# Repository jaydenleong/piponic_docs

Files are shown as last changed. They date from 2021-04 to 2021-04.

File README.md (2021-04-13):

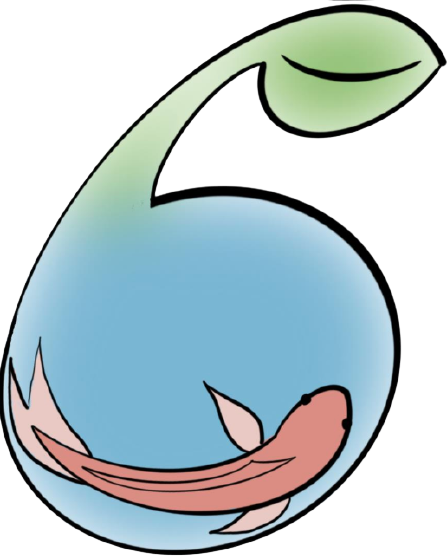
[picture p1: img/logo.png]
#  piponic_docs

## Project Description

This project aims to reduce urban food insecurity by reducing the cost and labour requirements of monitoring aquaponic or hydroponic food-growing systems. Designed specifically for hobbyist or small-scale growers, our project monitors critical system variables such as pH, temperature, and water-level and provides autonomous control. Critical notifications, real-time information, control settings, and system-history is available to users on a mobile application. 

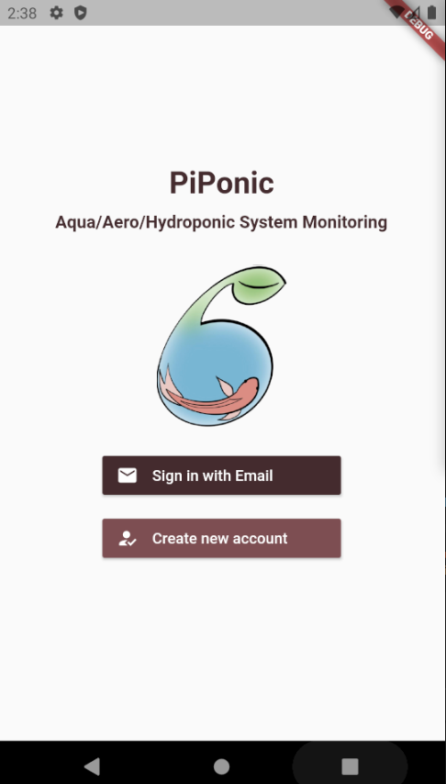
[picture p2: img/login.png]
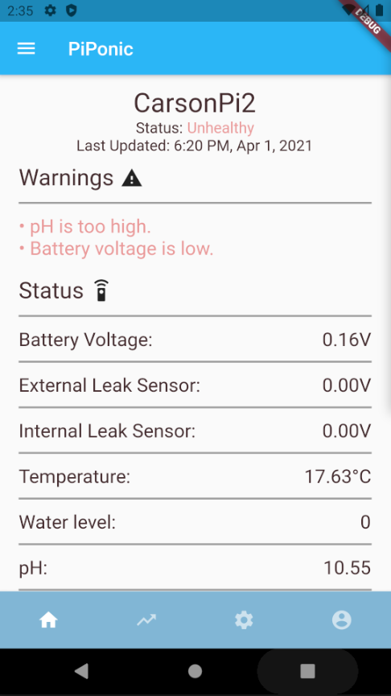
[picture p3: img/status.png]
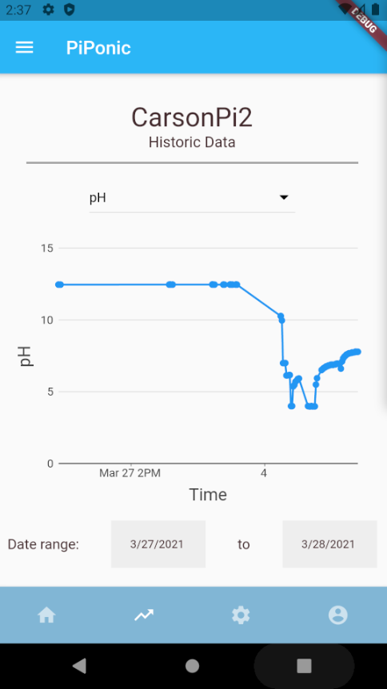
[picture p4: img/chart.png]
 &nbsp;&nbsp;&nbsp;  &nbsp;&nbsp;&nbsp; 

Our work contributes a low-cost, open-source hardware design, and IoT development framework that will allow hobbyists to expand and modify the system for their own needs. By simplifying the communication protocols, growers can focus on adding new sensors instead of worrying about data-security. 

Our system can also operate on battery power in the event of a power-outage, a critical failure in aquaponic systems. This feature allows growers to be notified and to begin to take corrective action within the minute of the outage.

## This Repository

Contains key documents describing our project. This includes the following (in the `docs/` folder): 

- System Installation
- User Manual
- Requirements
- Design
- Verification and Validation

Please consult those documents for more information about the project.

It also contains hardware modelling files, including: 
- Solidworks 2019 enclosure models (for layout)
- Altium Designer 2019 PCB and associated schematic files
- Gerber files associated with PCB design
- Bill of materials for PCB components

## Related Repositories

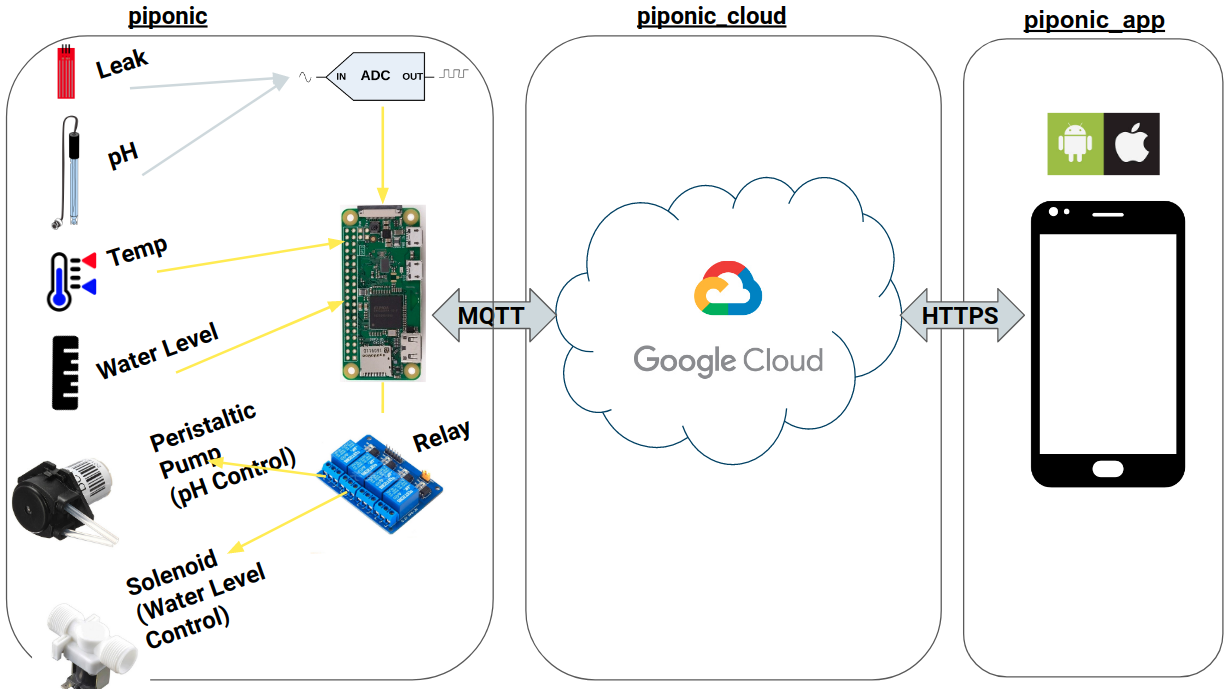
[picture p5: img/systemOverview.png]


- [piponic](https://github.com/jaydenleong/piponic): A sensing and control system for aquaponics or hydroponics. Runs on a Raspberry Pi and connects to the mobile application using this repository.
- [piponic_cloud](https://github.com/jaydenleong/piponic_cloud): Google Firebase functions that connect Raspberry Pis and the mobile application.
- [piponic_app](https://github.com/jaydenleong/piponic_app): The mobile application for users to remotely monitor and control their aqua/hydroponic installation. Implemented using Google's Flutter.

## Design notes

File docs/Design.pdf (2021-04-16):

# IoT Monitoring of Aquaponic and

# Hydroponic Food Production

# Design

### UBC Electrical and Computer Engineering Capstone 121

Carson Berry

Lynes Chan

Mason Duan

Jayden Leong

Hannah Xu

for

UBC SEEDS Sustainability Program

Bernhard Nimmervoll, UBC Mechanical Engineering

### April 16, 2021

## Revision History

Date | Author | Sections | Change
2020-10-05 | JL | 1.0 - 2.0 | Creation of document skeleton
2020-10-30 | JL | 1.0 - 5.0 | Added system overview and skeleton of subsystem sections
2020-11-29 | LC | 3.0 - 4.0 | Added the design decisions made for the sensors and the control devices
2021-02-19 | CB | 3.0 - 4.0 | Added details about power architecture, sensors, mounting, hardware, heat management
2021-02-20 | JL | 1.0 - 2.0 | Updated system overview to add brief overview of hydroponics and aquaponics, new system di-agram and updated purpose. Updated IoT sec-tion with details about the cloud implementation, along with other minor edits to microcomputer section.
2021-02-20 | MD | 6.0 | Updated software section to include use case di-gagram, screen explanations, and how the mobile application interacts with the back end.
2021-04-11 | CB | 3.0-4.0, 7.0 | Updated power design, sensor firmware, hardware design, added BOM tables, and ordering informa-tion.
2021-04-12 | JL | 1.0-2.0 | Added references and further detail to overview and background sections. Updated IoT section with references and implementation details.
2021-04-14 | MD | 6.0 | Updated software section to include final use case diagram design, screen explanations, and how the mobile application interacts with the back end.

## Contents

1 System Overview | 5
2 Internet of Things (IoT) | 8
3 Power | 15
4 Sensors | 18

5 Control Systems | 22
6 Software Application | 24
7 Circuit Integration - PCB | 33
8 Assembly | 34
9 Bill of Materials | 36

## 1 System Overview

Since our project is designed to work with both hydroponic and aquaponic systems, this section provides an brief introduction to both hydroponics and aquaponics. Afterward, the purpose of this project is given, and the high-level system design is described.

### 1.1 Hydroponics and Aquaponics

Hydroponics is a method of agriculture where plants are grown in a nutrient-rich aqueous solution [1]. Nutrients in hydroponics are inputted by the grower into the aqueous solution to nourish plants. This contrasts traditional forms of agriculture, where plants are grown in soil.

Aquaponics is very similar to hydroponics. In aquaponics, plants are also grown in an aqueous solution, however plants recieve nutrients in a different manner. Instead of growers inputting nutrients, plants recieve nutrients from fish waste [2]. To make this possible, fish are grown in separate tanks from the plants, with a filtration tank, and sump tank between them. Aquaponics recieves its name because of this, by being a mixture of aquaculture and hydroponics. A simplified diagram of aquaponics is show in Figure 1. Note that hydroponics systems look nearly the same, minus the fish tank.

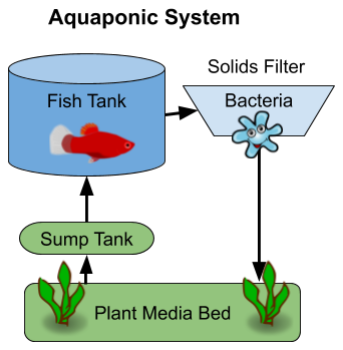
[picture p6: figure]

Figure 1: A diagram of a basic aquaponics system

### 1.2 Project Purpose

The goal of our project is to develop a system to monitor and control critical variables for hydroponic and aquaponic systems. In particular, our project focuses on monitoring water variables as they are most difficult to maintain at healthy levels in aquaponic and hydroponic systems. These variables include water pH, level, leakage, and temperature.

In terms of users, this system will be designed for small scale and hobbyist growers who maintain their aquaponic or hydroponic systems. Note that for this project, small-scale aquaponics or hydroponic systems are defined as systems with under 200 plants and under 3000 gallons of water. Since our users are small-scale growers and hobbyists, the system will utilize open-source and low cost technologies wherever possible to minimize barriers to usage and replication.

Please refer to the included Requirements document for further details about system requirements, background, and purpose.

### 1.3 High-Level System Design

Figure 2 below provides an overview of our design. As you can see, our design contains the following four subsystems: sensors, control, Cloud, and software application.

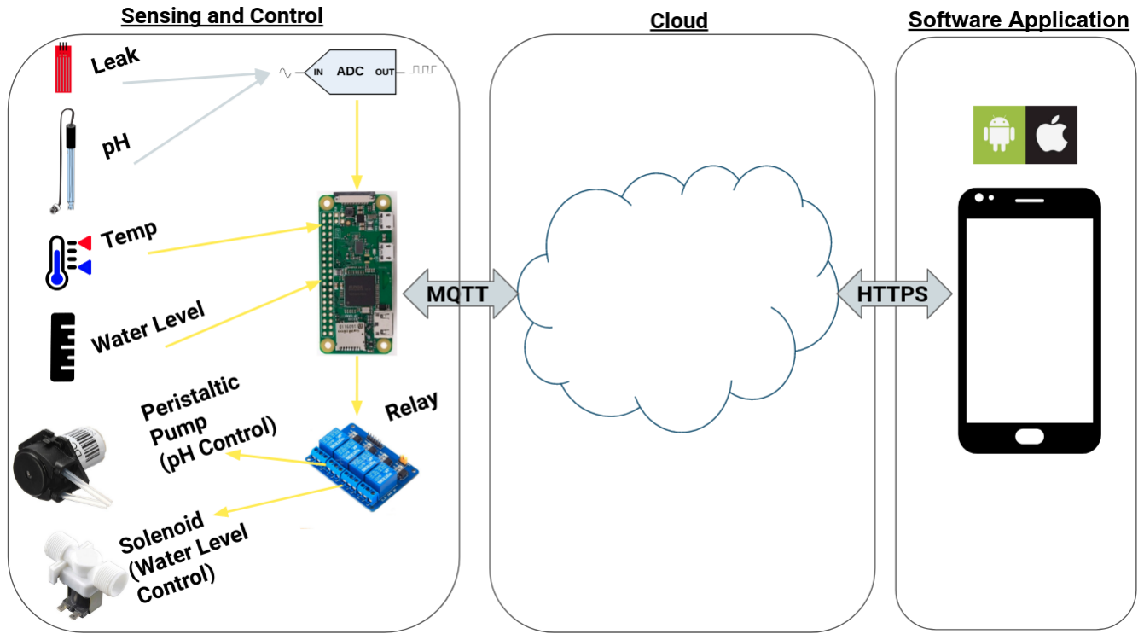
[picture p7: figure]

Figure 2: System Level Block Diagram

First, we can see the sensing and control subsystems in the “Sensing and Control”

block in Figure 2. This consists of a microcomputer attached to multiple sensors and control devices. As previously mentioned, there are four key sensors in our project shown: the water leakage, pH, temperature, and level sensors. These sensors allow our design to take measurements of the water of aquaponics or hydroponics systems. As such, the pH, temperature, and water level sensors are placed inside water tanks in an aquaponic or hydroponic system. As far as the control systems are concerned, two devices are attached to the microcomputer: a peristaltic pump and a solenoid. These two devices allow our design to automatically adjust pH and water level respectively.

Next, the Cloud subsystem is shown in “Cloud” block in Figure 2. This system’s responsibility is to transfer data between a mobile software application and the sensing and control system. It also stores past sensor measurements for later analysis.

Finally, on the software application is show in the “Software Application” block in Figure 2. This is where the user primarily interacts with their hydroponic or aquaponic system. This application displays past and current sensor measurements. It also allows the user to recieve alerts if urgent issues are detected by the sensing and control system, including issues like power failure and dangerous water pH levels.

In the following sections, the design of each of these subsystems will be explored in further detail.

## 2 Internet of Things (IoT)

The IoT subsystem recieves its name from the design decision to use internet communication to communicate with sensors and control devices installed on aquaponics or hydroponic systems. This enables our design to leverage advantages of internet communications. One key advantage is that the vast majority of our users have internet connected devices including laptops and mobile phones. Another key advantage is the ability for growers to monitor and control their aquaponics systems from anywhere they have internet connectivity.

The IoT subsystem, in our project, refers to all hardware and software needed to communicate between sensors and output devices and the software application. See Figure 3 for an overview of our IoT subsystem design.

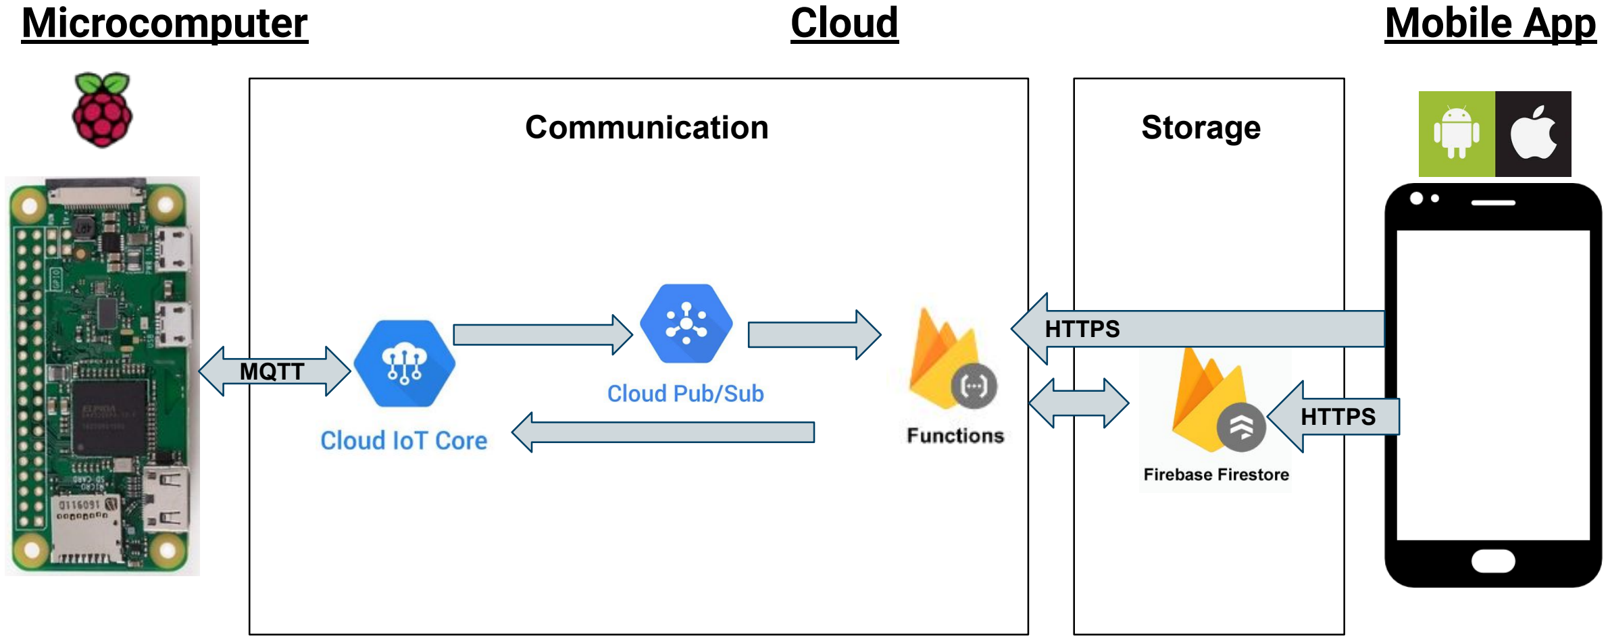
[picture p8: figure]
Microcomputer; Cloud; Mobile App; HTTPS; MQTT; Communication; Storage

Figure 3: IoT system overview

As seen in Figure 3, our IoT subsystem has 3 major components: the microcomputer, cloud, and mobile devices. The microcomputer and cloud components will be discussed in detail within this section. In the Software Application section, the mobile app component will be discussed further.

### 2.1 Microcomputer

There are two key functions that the microcomputer serves in our design. The first responsibility is to receive data from sensors, and to control output devices. The second responsibility is to send sensor readings to users, and to recieve commands for output devices from users. For each of these key functions, our team has made chosen design solutions to help address these issues. Consult Table 1 for a description of the key functions and their associated technological strategies.

Table 1: Description of microcomputer key functions and design strategies
Key Function | Req(s) | Design Solution | Reason(s)
Communicate with sensors and output devices | F1, F4 | Wired connection (e.g. SPI, IIC, GPIO), or wireless connection (e.g Bluetooth) depend-ing on the sensor or con-trol device | • Allows the flexibility to in-terface with many different sensors and output devices.
Communicate with user devices | F1, F2, F3, F6 | WiFi internet network connection | • Low cost compared other alternatives like LTE • High accesibility as hobby-ist and small-scale growers typically have a WiFi net-work setup within range of their system.

With these key functions in mind, our team selected a capable microcomputer. This microcomputer is the Raspberry Pi Zero W [3], shown in Figure 4.

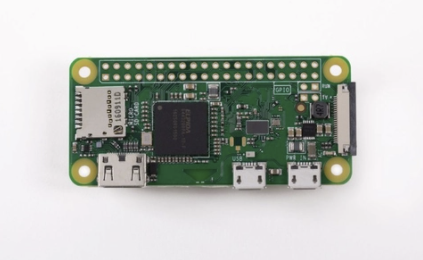
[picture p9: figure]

Figure 4: The Raspberry Pi Zero W microcomputer

The Raspberry Pi Zero W was chosen over other microcomputers that could perform the same key functions. This was done for the following reasons:

1. Low cost: costs around 40 CAD.
2. Wireless networking: supports both WiFi and Bluetooth.
3. Versatile: runs a Linux-based operating system called Raspberry Pi OS.
4. Documentation and support: Raspberry Pi is a popular platform with extensive tutorials, resources, and forums.
5. Interfacing: supports a variety of wired protocols including SPI, I2C. Also has 40 GPIO pins to interface with multiple devices.

Other notable microcomputers that were considered ESP32-based microcontrollers, and the Raspberry Pi 3B. However, the ESP32 was not chosen due to its more limited documentation and inability to run a linux-based operating system (making development slower). The Raspberry Pi 3B was not selected because of its similar functionality to the Raspberry Pi Zero W, but its higher cost of about 80 CAD.

Nevertheless, a final benefit of chosing a Raspberry Pi Zero W is that its software is compatible with other Raspberry Pi models, like the 3B. This gives design flexibility to optionally use more powerful or improved Raspberry Pi models other than the Raspberry Pi Zero W.

### 2.2 Cloud

The Cloud component of our IoT subsystem sits in between the microcomputer. Cloud in our project refers to cloud computing. This constitutes all the internet connected servers and associated IT infrastructure needed to communicate between the microcomputer (MCU) and the user’s mobile devices. As such, the cloud is responsible for the following:

- Relaying information between the MCU and user’s mobile devices
- Storing past sensor measurements
- Providing a software interface to the user’s mobile devices so they can access past sensor data and communicate with the MCU.
- Scaling to allow monitoring and control of multiple aquaponics or hydroponics systems from a single mobile device.

As such, the cloud contributes to meeting the functional requirements F1, F2, F3, and F6. Please refer to the Requirements document for details about these requirements.

As far as design solutions are concerned, we considered 2 key alternatives based on the above specifications. The first was using IT infrastructure as a cloud proxy to communicate between the microcomputer and the mobile application. The second choice was to communicate directly with the MCU, without any infrastructure in between. These options are summarized in Figure 5.

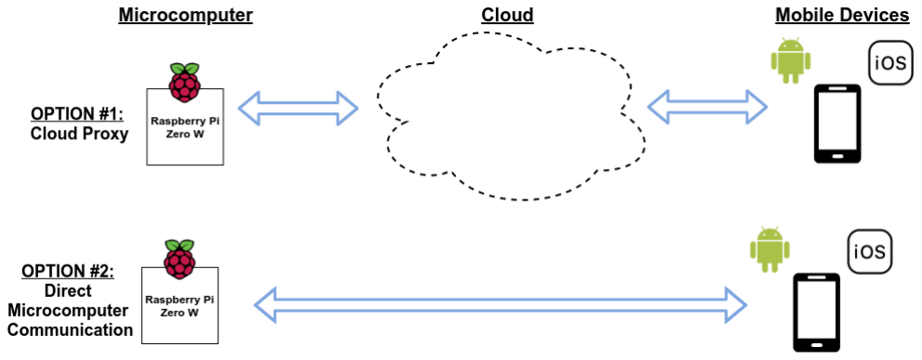
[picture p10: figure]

Figure 5: Two MCU to mobile application communication options.

To decide between these two main options, we weighed their strengths and weaknesses relative to their key functions. This comparison is summarized in Table 2.

Table 2: Comparison of MCU to mobile application communication options.
Function | Cloud Proxy | Direct MCU communication
Relaying information between the MCU and user’s mobile devices | Advantage: User devices can communicate the MCU anywhere with internet connectivity. | Advantage: No cost for proxy service. Disadvantage: User devices must be on the same local network as the microcomputer.
Storing past sensor measurements | Advantage: Cloud proxy services can automatically provision data storage to meet unlimited demand inexpensively. | Disadvantage: Users must be on the same local network as the MCU to access data.
Providing a software interface to the user’s mobile devices | Advantage: Cloud proxy services can offer APIs and pre-built tools to connect with mobile devices. | Advantage: communicating directly with an MCU can reduce software interface complexity and maintenance.
Scaling to allow monitoring and control of multiple aquaponics or hydroponics systems. | Advantage: Cloud proxy services offer automatic provisioning of resources based on demand | Disadvantage: limited to monitoring only systems on the same local network.

As seen in Table 2, the advantages of the cloud proxy option outweigh the direct MCU communication option. Most notably, the cloud proxy option offers more flexibility as it is not limited to being on the same private network as the MCU. It also is more capable of storing large amounts of past sensor data.

After choosing to use the cloud proxy option, we had a choice between 3rd party service providers, or managing our own cloud computing resources. We ultimately chose to use 3rd party IoT service providers over managing our own cloud computing resources for the following reasons:

1. Low cost: The estimated cost is less than 5 CAD/month.
2. High implementation speed: Service providers manage cloud computing resources, instead of developers needed to create and manage these from scratch.
3. Easy maintainance: Service providers typically provide web consoles for easy maintainability of resources.
4. Automatic scalability: Service providers automatically scale resources to match the amount of usage. For instance, more memory in a database is automatically provisioned.

Some popular 3rd party IoT service providers include Microsoft Azure, Google Cloud IoT, and Amazon Web Services (AWS) IoT. These service providers offer very similar services at comparable prices. So, our team decided to develop using Google Cloud IoT because it offered a better software interface to our mobile application.

This software interface will be discussed in further detail in the following sections. In addition, the architecture of our cloud system will be described in terms of two aspects: cloud communication and cloud storage.

### 2.2.1 Cloud Communication

Referring back to Figure 3, we see that the cloud communication component transfers data between the MCU and cloud storage. These components therefore help satisfy the functional requirements F1, F2, and F3, which require communication between the mobile application and the sensing and control system.

From Figure 3, we also see that the cloud commmunication part is made of 2 key components which are Google Cloud services. These are Google IoT Core, Google Cloud Pub/Sub, and Google Firebase Cloud Functions. See Table 3 below to see the role of each of these services in our design.

Table 3: Roles of Google Cloud communication services used.
Google Cloud Service | Role
IoT Core | • Provides an API for MCUs to communicate with Google Cloud using the MQTT protocol. • Provides MCU authentication and data encryption using public/private RSA keys
Pub/Sub | • Automatically recieves incoming messages from Google Cloud IoT core. • Allows Google Firebase Cloud Functions to respond to each message that is published by an MCU.
Firebase Functions | • Provides the ability to write functions that run on Google managed servers. • Writes MCU messages (with sensor data) in databases. These messages can then be retrieved by the mobile application. • Sends commands to MCUs through Google IoT Core.

Lastly, note that the communication protocol used between the MCU and Google Cloud IoT Core is MQTT. This was chosen over other possible protocols like HTTPs as it uses lower bandwidth and has less software overhead [4]. These two factors decrease the power consumption and data usage of our design.

### 2.2.2 Cloud Storage

Referring back to Figure 3, we see that the cloud storage components saves messages from both the MCU and the mobile application.

The key requirement satisfied by this section is F2, to be able to store past sensor measurements for analysis. However, like the previous section, the satisfy the functional requirements F1, and F3, which require communication between the mobile application and the sensing and control system.

Table 4 also shows another Google services that are used in our design: Google

Firebase Firestore.

Table 4: Roles of Google data storage services used.
Google Service | Role
Firebase Firestore | • Stores sensor measurements in a NoSQL format. • Stores MCU configurations.

Google Firestore is used for storage of past sensor measurements. This is because Google Firestore charges a cheaper rate for storage than other Google databases, making it preferable for storing large amounts of sensor measurement data [5]. It allows features a subscription model where new sensor readings are updated within our app as soon as they are stored in Firestore [6]. This allows us to display most recent sensor updates in near real-time.

Google Firestore also stores MCU configurations. When these configurations are updated, Google Cloud Functions automatically updates a device configuration. This is used to send commands to the sensing and control system from the mobile application. This design was chosen as it allows the mobile application to both read the current MCU configuration, and change it. That way, the mobile application can make configuration updates based on a MCU’s current status. For instance, if the pH level of a given MCU configuration is below the target value, it could be changed to a higher value by updating that MCU’s configuration.

### 2.2.3 Cloud System Implementation

As mentioned in section 2.2.1 above, Google Firebase Cloud Functions are used to save sensor messages, and connect IoT devices to the mobile application. So, just as depicted in Figure 3, Google Firebase Cloud Functions are central to the cloud system and define much of its functionality.

The implementation of this project’s Google Firebase Cloud Functions can be found in the piponic cloud repository (https://github.com/jaydenleong/piponic_cloud). The README of this repository also provides further documentation about how the overall cloud system can be setup and maintained.

## 3 Power

Our system is comprised of various electric components, including the Raspberry Pi microcomputer, sensors, and output devices. Power for the system will be available from two sources, a main, and a backup. The main power source is 12V DC. This is supplied by a commercially available power supply that rectifies and steps-down voltage coming from a 120V wall outlet. This will provide power to the sensor hub during normal operation. That is, when the device is plugged in, and the line-voltage is available.

### 3.1 Back-up Power

The backup power will be provided by a battery pack with 2 AA batteries, with voltage boosted to 5 V from a DC-DC boost converter. The arrangement of these two inputs can be seen in figure 6. 3 AA batteries could also be used in series to produce a voltage of 4.5V, which will increase the lifespan of the back-up power system and the efficiency of the boost-converter chip. If this arrangement of batteries is used, a voltage divider must be added to the battery-voltage monitoring circuit, so that the maximum voltage of 4.5V is read at max 3.3V. We recommend using 100k and 36.9k resistors for this voltage divider to minimize power loss.

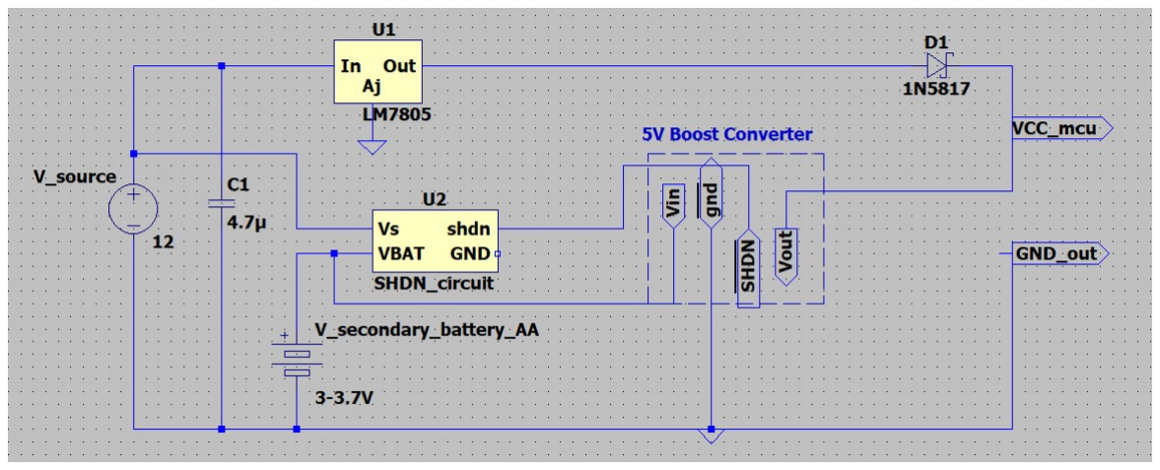
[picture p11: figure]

Figure 6: Uninterruptible power supply architecture.

The LM7805 voltage regulators are responsible for delivering all of the current used by the 5V devices during normal operation. It has been observed that all of the 5V devices consume around 200mA during normal operation, and the voltage regulators are rated to 1A. To increase the safety margin associated with heat-burnout, a 15g aluminum TO-220 heat sink was added to the LM7805 chip. Two LM7805 regulators are used in parallel to ensure adequate power is always available. This was also added to the Schottky diode at the output of the LM7805 chip.

To conserve the battery-lifespan, the boost converter is turned off automatically when the 12V line voltage is present. The circuit that accomplishes this can be seen in figure 7 - a simple BJT switch application. In the event of a power failure, the system will be able to run for 8 hours on backup power. This functionality is intended as a way to keep monitoring the condition of the aquaponic or hydroponic systems in the event of a power failure.

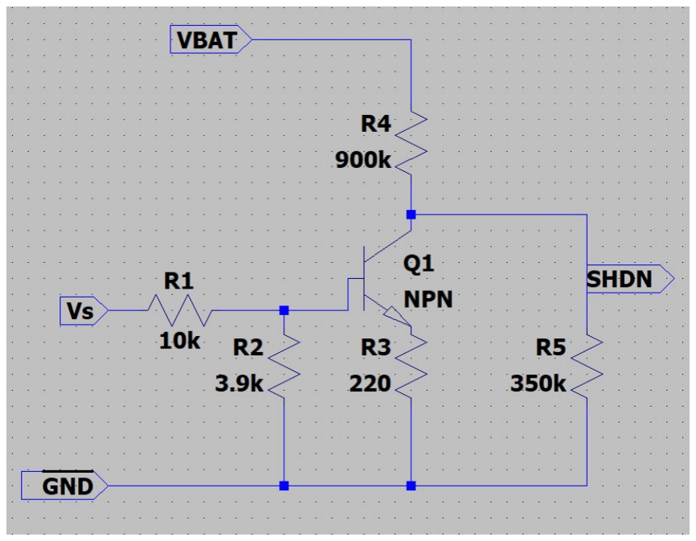
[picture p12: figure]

Figure 7: Boost converter shutdown circuit. This circuit disables the AA batteries when 12V is present.

For boosting 2 AA batteries up to 5 V, the Pololu 5V Step-Up Voltage Regulator U1V11F5 is a high quality, low cost, easily accessible option that can be implemented by hobbyists with minimal difficulty. It can take anywhere between 0.5 and 5 V input and will automatically boost it to 5.02 V output.

### 3.2 Power Budget

Our monitoring system consumes on average 810 mW when on back-up power. Most of this comes from the operation of the raspberry pi. A breakdown of the average power use can be seen in figure 8.

The control devices and relays operate only when line power is available (that is, when not on back-up power), and when all control devices are active the system consumes an additional 5W.

### 3.3 Current Protection

The output voltage will be connected via Schottky diode to the line voltage in, before being connected to the Raspberry Pi. This will effectively OR the voltage source seen by the Raspberry Pi. Several other circuit topologies were simulated and tested, and the Schottky diode topology represents the best functionality in both

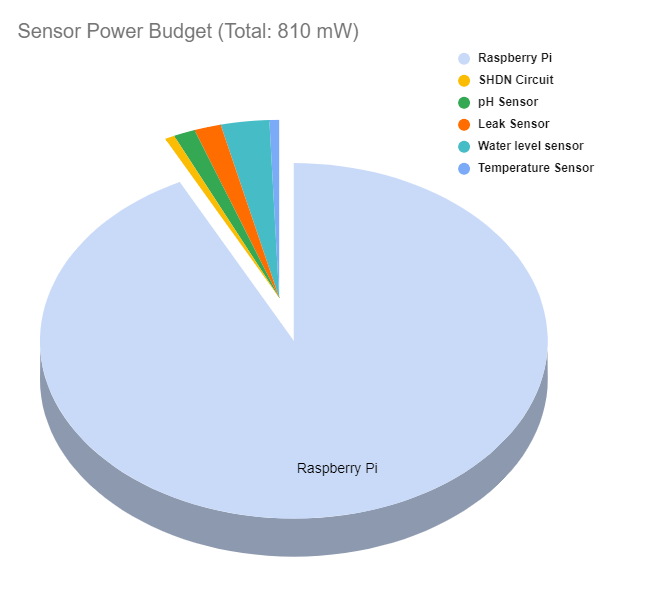
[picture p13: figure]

Figure 8: Average monitoring system power breakdown.

Table 5: Power current protection device comparison.
Device Type | Current Protection | Power Loss | Line Voltage | Backup Voltage
N Mosfet | No | 2 mW | 5 V | 5 V
P Mosfet | Yes | 2 mW | 5 V | 4 V
Schottky Diode | Yes | 60 mW | 4.7 V | 5 V

normal operation and backup power mode. The other topologies that were modelled prior to making the design decision were a P-channel mosfet or an N-channel mosfet.

The N-channel mosfet does not achieve the desired functionality of 1-way current protection, so this solution is disregarded. The P-Channel mosfet does an excellent job minimizing power loss, however in the back-up power scenario, drains an unacceptable amount of current such that the line voltage will be 4V, which is too low for our applications. Therefore, the best solution is the schottky diode, despite its relatively high power consumption, because it keeps the line voltage at an acceptable level in both operating conditions.

This system is intended to be used with a LiPo battery pack as a backup battery source, however due to safety considerations, the implementation of this will be limited to a recommendation and design only. If one is using LiPo batteries to provide backup power, please familiarize yourself with the appropriate safety procedures associated with using LiPo technology.

For keeping a LiPo battery fully charged while plugged in, and boosting the voltage a 3.7V LiPo cell to 5V when using, the PowerBoost 1000 Charger by Adafruit is our recommended breakout board. It supports load-sharing which means the board can supply power to the hub at the same time as charge the battery. It accomplishes this with 2 special ASICs. The input line voltage can be directly input into the PowerBoost 1000, which will automatically manage OR-ing the power for the Raspberry Pi.

## 4 Sensors

Our design is centered around 4 types of sensors: Temperature, pH, water-leak, and water level. These sensors focus on the the status of the water in the system because this will effectively address the needs of fish, plants, and microbes, as water is the media through which these species interact.

### 4.1 Sensor Type Selection

There are many distinct indicators of ecosystem health when monitoring a hydroponic or aquaponic system [7]. There’s aqueous concentration of carbon dioxide and oxygen. There’s accumulation of bio-solids from fish waste in the water. There are three different important types of dissolved nitrogen: nitrate, nitrite, and ammonium. The alkalinity and pH of the water are both very important as well. The water level, flow-rate, and temperature are not to be overlooked either.

Implementing a system that monitors all of these important summary variables is possible, however would require significant investment of both time and money. Limited as we are in both time and money, we decided to focus on the most important, the lowest cost, and the easiest to implement sensors.

By building our project with simple sensors, we make our design accessible to as many people as possible. Our sensor-framework can easily be expanded upon by future developers or users, who can choose to purchase more expensive sensors if they wish to.

We identified 4 types of sensors that fit the above criteria

1. pH
2. Temperature
3. Water-level
4. Water-leak

The other sensor types were either too expensive or did not add enough valuable information to the monitoring system for them to be considered.

### 4.2 Analog to Digital Conversion

The Raspberry Pi does not have an analog to digital converter (ADC) built in. Several of the sensors that are being used, and that future designers could use will require the use of an ADC, so we added one to our project. The ADS1115 is a 16 bit, 4 channel, programmable gain, I2C ready ADC, which can operate between 3.3 and 5 volts. These specifications meet the needs of this project by maximizing resolution, minimizing pin use, minimizing power consumption, and having sufficient channels. The ADS1115 was designed to be a very power-efficient board by

Currently 4 of the ADC channels are being used, leaving 4 free for new features. The current channels in use are:

- External Leak Sensors
- Enclosure Internal Leak Sensors
- pH Sensor
- Battery voltage

The pins of the Raspberry Pi are designed to operate at 3.3 V, however have large enough pull-up and pull-down resistors that they can handle 5V as well. To maximize longevity, and minimize chance of pin burnout, the ADS1115 ADC is operated at 3.3V.

By operating the ADC at 3.3V, the maximum voltage it can read from one of its input channels is now 3.3V also. If any component cannot run at 3.3V, then it must be reduced to 3.3V from it’s higher voltage (such as 5V) so as to not damage the ADC. This can be accomplished with a voltage divider.

### 4.3 Temperature

Temperature is important in aquaponic or hydroponic growing systems because different species all have their own preferred temperature range. If a user is growing multiple species in a single system, they may wish to control the temperature so that all of the species they are growing are within the functional temperature limits.

We considered three types of temperature sensor. We chose DS18B21 ($10) temperature sensor over the DS18B20($5) and I2C BME280($20) temperature sensor. This decision was made because:

- The DS18B21 provides temperature values every minute and allows the Implementation of a system that can display values in real time. Requirement: F1

- The DS18B21 is waterproof and the other alternatives are not. Choosing this sensor leads to a system that is water resistant. Requirement: NF4
- The DS18B21 is in the mid price range and contributes to an affordable system. Requirement: NF1

The temperature sensor communicates over 1-wire interface with the Raspberry Pi. The Raspberry pi operating system has convenient protocols for 1-wire interfaces that automatically receive the data from these devices and store them in a given location in memory. The script that reads the temperature, quite simply, checks this location in the memory for the temperature, and performs some simple cleanup.

### 4.4 pH

In hydroponic and aqauponic systems, the pH has been described by experts as the Master Variable [7]. This means that it controls or influences many metabolic processes. It is essential that the pH of the system does not go outside of the maximum or minimum tolerable limits of the organisms present in the growers system.

For these reasons, we deemed the pH to be an essential part of our monitoring solution.

We considered many types of pH sensors among many and initially chose the PH-4502C($39) over the LeoEc($60) because:

- The PH-4502C is a low power sensor (less than 0.5W) and will therefore provide better lifespan in the event of a power failure. Requirement: F5
- The PH-4502C provides pH values with a delay of 0.5s. Requirement: F1
- The PH-4502C is lower priced compared to the LeoEc and middle priced compared to other pH sensors that don’t meet our requirements. This choice contributes to an affordable system. Requirement: NF1

The PH-4502C is intended to be used by mapping pH 7 to 2.5V, 14 to 0V, and pH 0 to 5V. These values rarely seem to be present in reality, necessitating significant calibration.

This pH sensor performed poorly in testing, and so another type of pH sensor was purchased; the SEN0161-V2 from DFRobot. This electrolytic pH probe works on the same principle of the one above but has a different amplification board that does not have any mechanical calibration requirements. It also meets all of the other requirements outlined above.

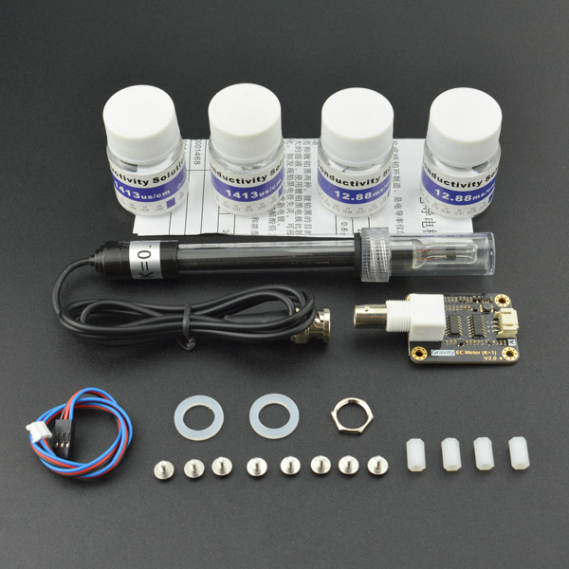
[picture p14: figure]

Figure 9: pH sensor Kit

### 4.5 Water Level

Measuring the water level enables growers to ensure that they have adequate water in their system for their plants and fish. If the water level is too low the system can heat-up quickly or change in temperature or chemical concentration. The water level is measured with the intention of automating the water refilling process.

There are different ways to measure the water level. We chose the Binary Water Level Detector, SEN0204-ND ($13). The other alternatives are the Ultrasonic Sensor, HC-SR04 ($4) and the E-tape Liquid Level Sensor ($60).

We made this decision because:

- The SEN0204-ND provides the minimum data to maintain a desired water-level F1
- The SEN0204-ND is small and can scale very well to differently sized systems. This makes the sensor easier to install on many more types of aquaponics systems compared to alternatives. NF5
- The SEN0204-ND is low cost. The HC-SR04 and other Ultrasonic Sensors have a very short lifespan and break very easily, especially in environments where water is involved. So in the long term, the SEN0204-ND contributes the most to an affordable system as it is IP67 rated. NF1, NF4

### 4.6 Water Leak Sensor

For indoor aquaponic or hydroponic systems a leak may be a catastrophic failure that could cause significant property damage or could result in eviction of the grower(s). Detecting leaks, is therefore of paramount importance to ensuring long-term social sustainability of aquaponic or hydroponic systems in urban environments.

Leak sensors could be implemented in many ways. We chose a very low cost hobbyist leak sensor available online as seen in figure 10.

In our design, this sensor is also placed inside the enclosure to detect if any of the system electronics may be compromised.

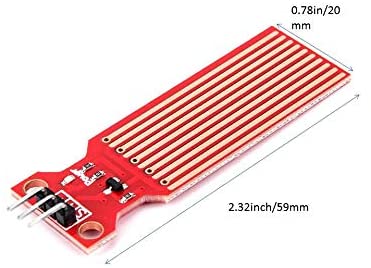
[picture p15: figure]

Figure 10: Water leak sensor

We made this decision because:

- The leak sensor provides the minimum data to detect a leak, and can be read continuously by the ADC. F1, F3
- This sensor is low cost. NF1, NF4

## 5 Control Systems

We considered 3 types of output devices: Air pump to oxygenate the water, Water pump to control the water levels, and the pH adjuster to control the pH levels

### 5.1 Air Pump

Introducing oxygen to a system can be done by creating movement in the water. This is normally done by having an air pump create movement within the tank. The problem arises due to the scope of our project. The air pump needs to work for systems of up to 3000 gallons of water. There is too much variability in the size of the system and introducing an air pump complicates this control system greatly. We have decided not to include this within the scope of our project.

### 5.2 Water Pump

We considered having a simple control system that would automatically keep the desired water level with the use of water pumps. Once we focused on the scope of our project, a water pump is not ideal being controlled through the RaspberryPi due to 2 reasons. The first reason is that the scope of our project is to design for systems up to 3000 gallons of water. Installing a water pump system suitable for a RaspberryPi would be unreasonable due to the relatively small pumps available through the RaspberryPi. The second reason is if we were to install a reasonably size pump, this would take far too much power for our entire system to work in parallel with this pump.

### 5.3 pH Adjuster

There are two ways to change and maintain the pH levels of the system: with a liquid solution or a solid object usually peat moss or driftwood. We have chosen to use the liquid solution and have decided to use a Peristaltic Pump ($12) to control this liquid solution due to the following reasons:

- The solids can produce discolouration in the water. This will not only make physical observation harder, a feature we might implement is a waste detecting system, and discolouration affects that. The liquid solution will not interfere with the appearance of the system and provide accurate values in real time. (F4)
- The liquid solution is a lot easier to measure. The volume of a liquid is much easier to measure and transport compared to something solid. This results in a much easier installation. (NF2, NF5, NF7)
- The Peristaltic Pump is cheaper and easier to design compared to something that needs to transport a solid. This leads to an affordable system (NF1, NF2)
- There are many types of liquid solutions that can be used while the solids needed are very specific and usually hard to find. This allows users to customize more easily compared to the solids. (NF5, NF7)

The peristaltic pump will pump a basic solution into the aquaponic or hydroponic system to raise its pH, because in most aquaponic system, the bacteria acidifies the water. We recommend that the solution to be pumped into the system is potassium hydroxide and calcium hydroxide in an alternating manner to provide some micronutrients as well as pH buffering.

## 6 Software Application

To implement the software application to display the aquaponic’s data to the user, we considered various aspects, like the technology we were going to use, how we were going to implement said technology, and the trade-offs we made for each decision.

### 6.1 Technology

The two main technologies we considered to implement the software application were web and mobile. We ultimately choose to use a mobile based approach to implement our software application than a web based approach. The main factor that that determined this decision was ease of use. In a mobile based approach users would be able to quickly access the application, as user preferences are saved and tied in with the mobile application. This means that the user doesn’t have to re-authenticate time after time when trying to access their aquaponics data. Another big factor we considered when choosing a software approach was accessibility. Almost everyone has their mobile devices on them at any given time during the day, which would provide greater accessibility to the application. A final consideration that we explored was push notifications. With a mobile based approach, we are able to send push notifications to users when extremely urgent matter arises, whereas in a web based approach this isn’t even an option.

### 6.2 Implementation

We considered many different options we could take to create a mobile application. We debated on whether or not we would want to create a native application or build one with a cross platform language. Given the time and nature of this project, we ultimately decided on a cross platform approach. With a cross platform approach, we would be able to develop for both Android and IOS with half the effort and half the code base. One of the draw backs however is that we might lose niche native functionality specific to either Android or IOS. Since our software application is simple, we believe that the niche native service loss wouldn’t be detrimental to the project. We choose Flutter as the our cross-platform language to implement this mobile application over other cross platform languages such as React Nastive, or Xamarin since Flutter allows for quick implementation of native feeling applications.

### 6.3 Use Case Overview

Upon entering the application, the application checks if the user has previously been authenticated. Here users can authenticate themselves by either signing up or signing in. Upon successful sign in or creation of an account, the user would be taken to the application’s home screen. The ability to authenticate users to access to their account and aquaponioc system meets our non-functional requirement NF2.

The home screen displays a summary of one of the existing systems that the user has registered with the application. The summary includes the name of the system, the status of the system, last time the information was updated, the warnings for the system, and a list of all the sensors and it’s measured values. The summary of the aquaponic system on the home screen meets our function requirement F1. From the home screen, the user is able to navigate to the sensor chart screen, the aquaponic system settings screen, and the user setting screen.

The sensor chart screen displays historic measurements made by the sensors on a chart. The user is able to select which sensor to view and the date range in which the measurements were taken. The ability to view historic sensor measurement within a given date range meets our function requirement F2.

The system settings screen allows the user to set the range of acceptable values for the aquaponic sensors and well as calibrate the pH sensor. The user can also change the sensor measurement interval on this screen. The ability to adjust and calibrate sensors meets our functional requirement F3.

The user setting screen is where the user is able to logout or delete their account if they so choose. In the user setting screen, the user is also able to add additional aquaponic systems to their account provided they know the aquaponic systems identification. The ability to add and monitor additional aquaponic systems meets our non-functional requirement NF5.

If the user is already logged in the application, the user may receive notifications if one or more of their aquaponic system is in a critical state. Upon tapping the application, the user will be brought to the home page with the summary of the system in the critical state. The ability to send alerts to growers when a aquaponic system enters a critical state fulfills our function requirement F3.

An overview of how the user can interact with the software application is highlighted and illustrated in the use case diagram below in figure 9.

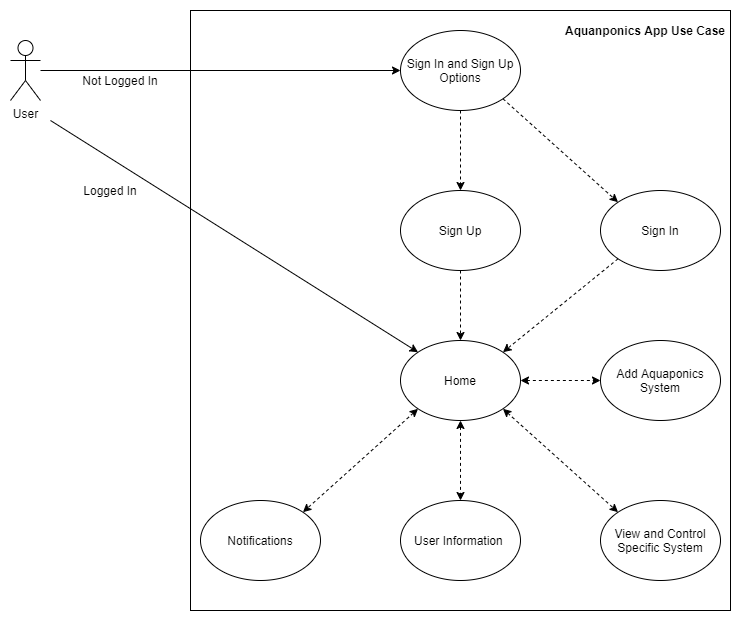
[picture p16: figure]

Figure 11: Use Case Diagram

### 6.4 Screens

Below are the different screens in the software application and an explanation of their intended user interactions as well as how they interact with the overall IOT infrastructure.

### 6.4.1 Sign In and Sign Up Options Screen

The sign in and sign up options screen will be presented to users who aren’t previously authenticated on the application. The sign in and sign up options screen will give the user the option to either Sign Up an account or login to an existing account. The user can Sign Up with the application by providing an email and password or by Signing in using a valid Google account. An image of the application’s sign in and sign up options screen can be seen below in figure 12.

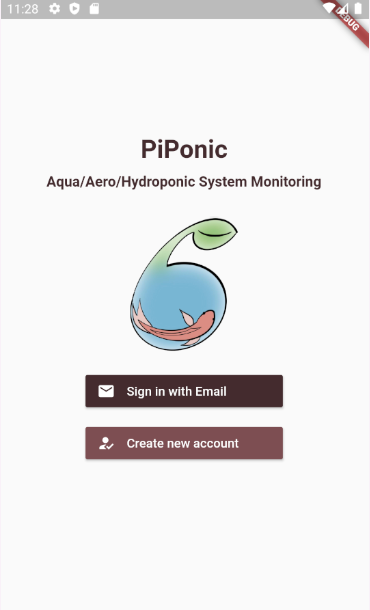
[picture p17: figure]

Figure 12: Sign In and Sign Up Options Screen

### 6.4.2 Sign In Screen

The sign in screen is presented when the user taps on the ”Sign in using Email” option in the sign in and sign up options screen. This page contains two input fields for the email address and password. Unsuccessful authentication submissions won’t let the user into the application whereas successful authentication submission will direct users to the application’s home screen. Each login attempt will trigger a request to Firebase to confirm the users credentials and to get the user’s unique User ID. The email input box verifies that it’s a valid email address by checking if the ’@’ character is present within the email submission. Similarly password input box verifies that the password is sufficient by the password length is at least 6 characters. An image of the sign in screen can be seen below in figure 13.

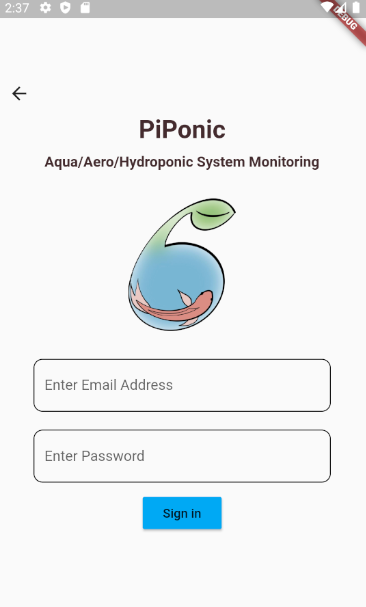
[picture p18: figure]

Figure 13: Sign In Screen

### 6.4.3 Sign Up Screen

The sign up screen is presented when the user taps on the ”Sign up with Email” option in the sign in and sign up options screen. This page contains two input fields for the email address and password. Unsuccessful sign up submissions won’t let the user into the application whereas successful sign up submission will direct users to the application’s home screen. Each login attempt will trigger a request to Firebase to create the user account by using the submitted user credentials and to get the user’s unique User ID. The email input box verifies that it’s a valid email address by checking if the ’@’ character is present within the email submission. Similarly password input box verifies that the password is sufficient by the password length is at least 6 characters. An image of the sign up screen can be seen below in figure 14.

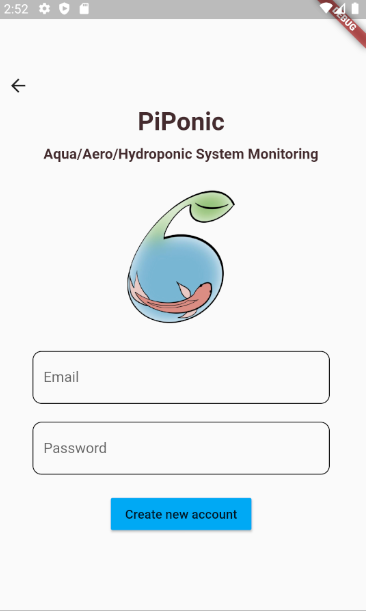
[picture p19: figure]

Figure 14: Sign Up Screen

### 6.4.4 Home Screen

The home screen is presented when the user successfully authenticates with the application. If there are existing aquaponic system(s) associated with the users account, the home screen will show a summary of one of the existing systems. The home page would show a summary of the chosen system including the name of the system, the status of the system, last time the information was updated, the warnings for the system, and a list of all the sensors and it’s measured values. The values are of the aquaponic system is directly tied to the Firebase backend; this means that the values on the home page will update in real time whenever a there is a new reading in the Firebase backed. Am image of the home page can be seen below in figure 16.

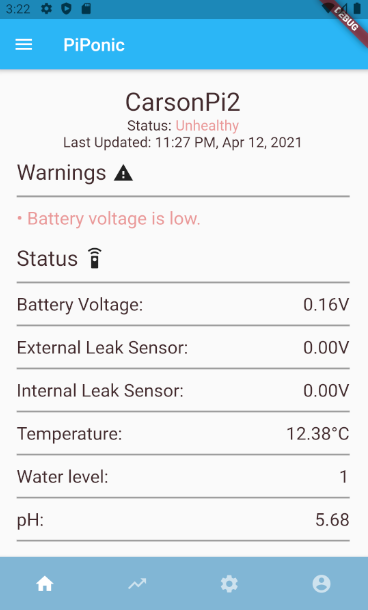
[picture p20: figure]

Figure 15: PiPonic home screen

### 6.4.5 Aquaponic/Hydroponic List

Tapping on the hamburger menu button on the top left of the application, the list of the user’s aquaponic systems will slide out. Here the user is able to switch between the different aquaponic systems associated with their account. The list of the aquaponic systems is directly tied to the Firebase backend; this means that the list of aquaponic systems will change in real time whenever a there is a change to the users access to different aquapnic systems.An image with the location of the hamburger menu button and the list of the user’s aquaponic systems is shown below in figure 14.

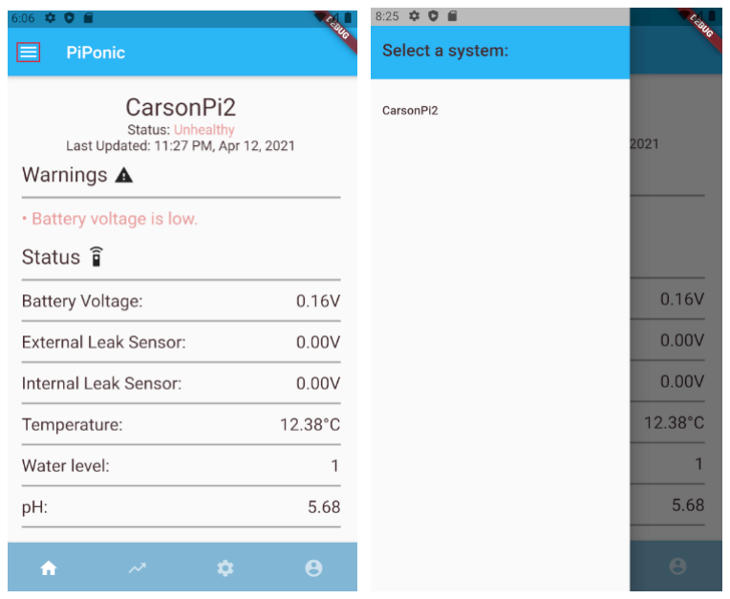
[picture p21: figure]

Figure 16: Location of the hamburger menu button and the list of the user’s aquaponic/hydroponic systems

### 6.4.6 Chart Screen

Tapping on the rising trend icon in the bottom navigation bar brings the user to the chart screen where the user is able to see a chart of their sensor values and the time at which they were measured. Here the user is able to change the different sensors that they want to see and are also able to change the range of time for which the measurements were taken. New measurements are queried from the Firebase backend and the graph is changed whenever a user changes a sensor to view or changes a time range. A screenshot of the charts screen can be seen below in figure 15.

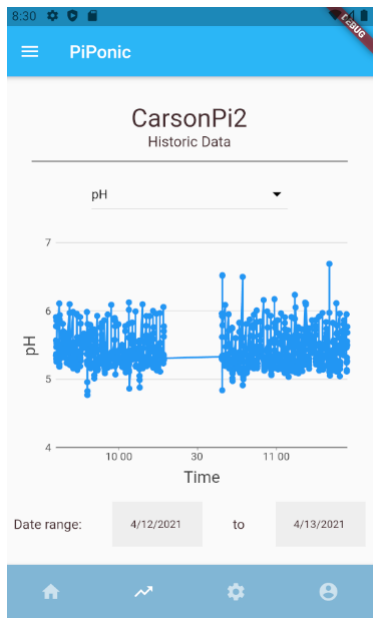
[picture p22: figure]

Figure 17: PiPonic Chart Screen

### 6.4.7 System Settings Screen

Tapping on the gear icon in the bottom navigation bar brings the user to the aquaponic system setting page. Here the user can set the range of acceptable values for the aquaponic sensors and well as calibrate the pH sensor. The user can also change the sensor measurement interval in the ”General” tab. When the user enters a new acceptable range or calibrates the pH sensor or changes the sensor measurement interval, the application will update the backend which would then update the system of the new changes. A screenshot of the aquaponic settings screen can be seen below in figure 16.

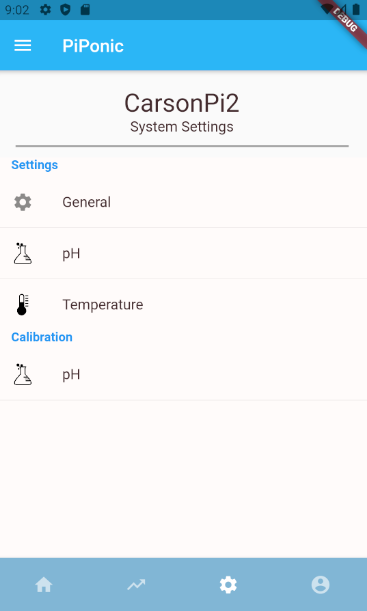
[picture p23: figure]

Figure 18: PiPonic system settings screen

### 6.5 User Settings Screen

Tapping on the user icon in the bottom navigation bar brings the user to the user settings page. Here the user can add additional aquaponic systems to their account to monitor and control. When the user adds additional aquaponic systems to their account, the application would then notify the backend which would then associate the new aquaponic system with the users identification. The application would then automatically add the new aquaponic system in the users application. The user can also logout of their account and delete their account. A screenshot of the user settings screen can be seen below in figure 17.

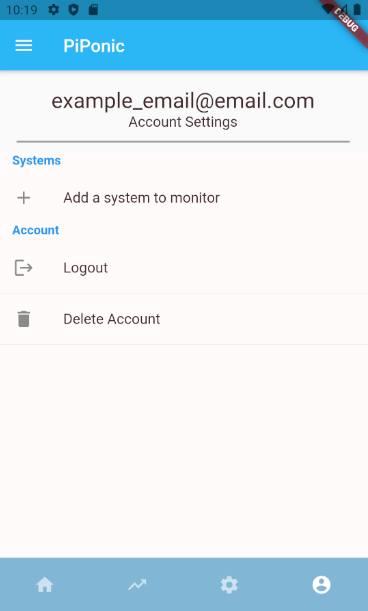
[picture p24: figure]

Figure 19: PiPonic user settings screen

### 6.5.1 User Information Screen

The notification screen is presented when the user clicks on the user icon in the bottom navigation bar. The user screen shows the user information and allows for the user to log out of the application or delete their account.

### 6.5.2 Add Aquaponics Screen

The add aquaponics screen is presented when the user clicks the profile icon in the bottom navigation bar. The add aquaponics screen contains input fields that pertains to the aquqponic system they are trying to add. Upon successful submission of results, the aquaponic system will be created in the Firebase back-end and linked with the users User ID.

## 7 Circuit Integration - PCB

In order to maximize simplicity and repeatability of construction, robustness, and lower production costs, a custom printed circuit board was designed. This element integrates several circuit elements, including the power supply architecture, reading from sensors, sending control signals to the relay module, and interfacing with the Raspberry Pi. The PCB design can be seen in figure 20.

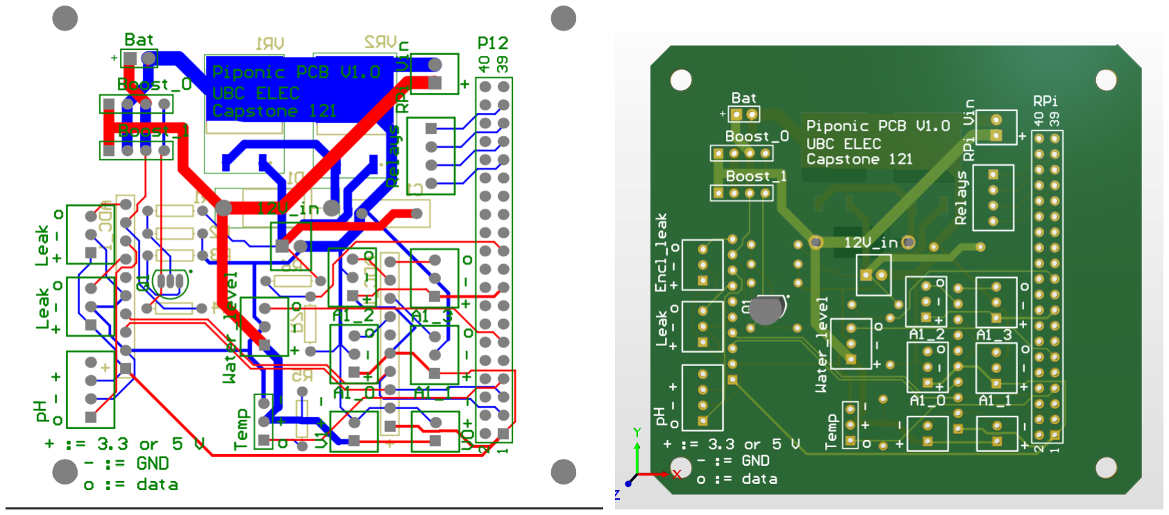
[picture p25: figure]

Figure 20: Custom PCB Layout

The integration with the raspberry pi is accomplished by having this PCB take the format of a ’hat’. This means that the board will directly mount onto the Raspberry Pi’s male header pins, so that no mistakes can by made by the user in wiring.

All sensors will integrate with the PCB through simple board-mounted screw-down terminal blocks. Although this adds to the size of the final design, it is the simplest for users.

### 7.1 Component Choices

The components for this PCB were chosen to make manufacturing without a solderreflow station easy - so almost all of the components are through-hole. The only exception to this are the voltage regulators, which are chosen as SMT components for the built-in heat-dissipation, and for the low profile allowing them to be mounted to the underside of PCB, which will allow for the PCB to have a much smaller footprint.

### 7.2 Future Development Considerations

This PCB was designed with future development in mind. It features 8 total ADC channels, 4 of which are unused. These ADC channels can be used for additional sensors. It has 2 unused relay-channels for additional control devices. All of the Raspberry Pi header pins are still accessible with this design, so that any type of device or communication channel may be added through jumper wires by future users.

## 8 Assembly

In consideration of the construction of the system, the NF4, NF1 requirements were chiefly considered. That is, that the design is waterproof and low-cost.

All components were roughly modelled in Solidworks 2019 to gauge how large the enclosure needed to be. Models of all necessary components can be seen in figure 21 and 22.

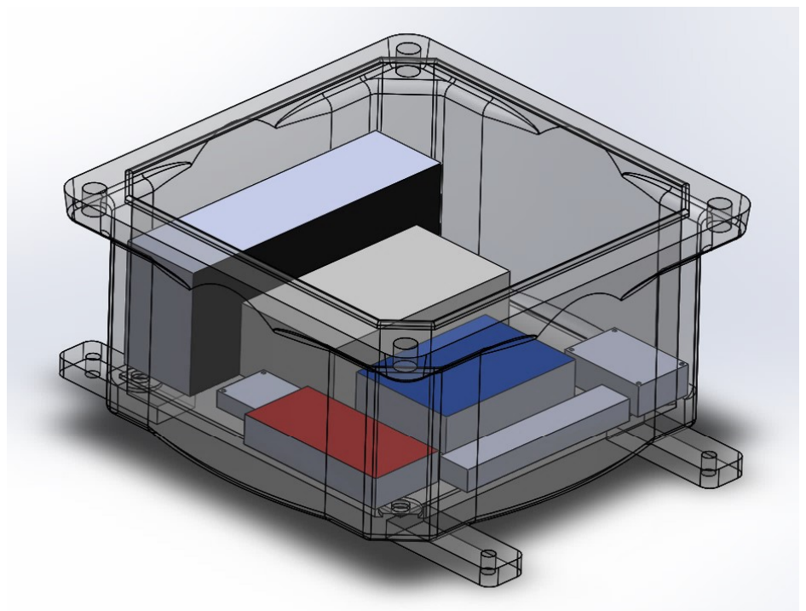
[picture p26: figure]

Figure 21: Enclosure elements inside enclosure: Power Supply, Breadboard, Relay Block, Terminal Block, Raspberry Pi, Water-level board, pH sensor board.

There are 5 independent wire ports that must penetrate the enclosure in a waterproof

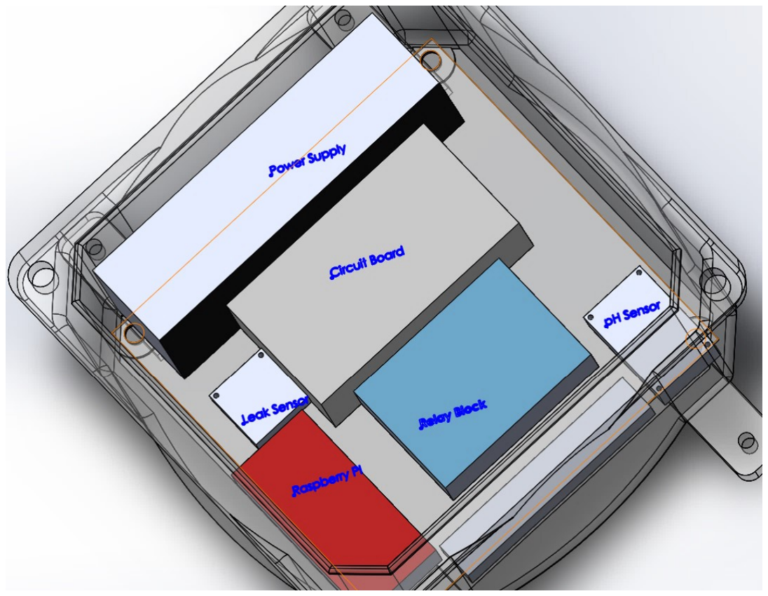
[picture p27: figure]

Figure 22: Labelled Enclosure elements: Power Supply, Breadboard, Relay Block, Terminal Block, Raspberry Pi, Water-level board, pH sensor board.

manner. To accomplish this, waterproof nylon cable glands were used. An example of one of these can be seen in figure 23. These devices have a rubber seal which is compressed around a wire inside it, forming a seal.

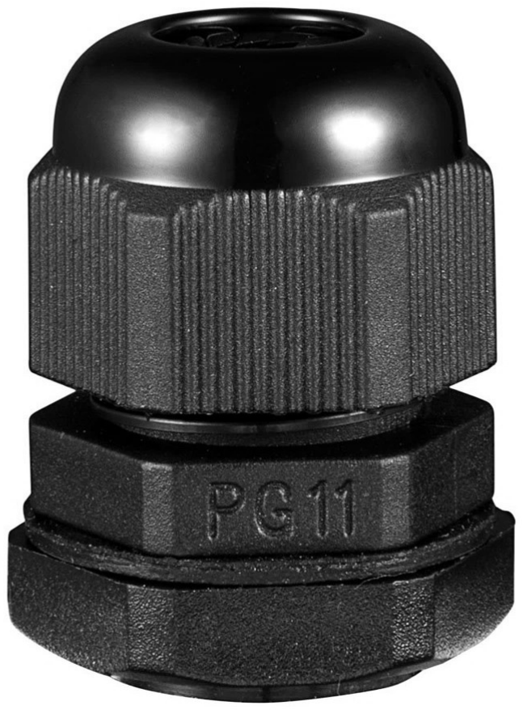
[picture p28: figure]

Figure 23: Waterproof Nylon Cable Gland example.

For ease of maintenance and durability, all of the electronic components are mounted to a board that are mounted to the corners of the main enclosure with double-sided tape. This board is constructed from 1/2” plywood.

## 9 Bill of Materials

In order to reconstruct this project, one will need to purchase many components. The sources for these are outlined in this section and in the Installation Instructions document.

### 9.1 Hardware

The hardware BOM can be seen in the table below.

Designator | Description | Quantity | Link
Enclosure | 8x8x4’ junc-tion box | 1 | https://www.homedepot.ca/product/1000403713 (https://www.homedepot.ca/product/carlon-thermoplastic-junction-box-8x8x4-in/1000403713)
Heatshrink | Variety Pack | 1 | https://leeselectronic.com/en/product/15370-kit-heatshrink-variety-pack-170pcs. html (https://leeselectronic.com/en/product/15370-kit-heatshrink-variety-pack-170pcs.html)
Cable Gland | 7mm | 3 | https://leeselectronic.com/en/product/html (https://leeselectronic.com/en/product/61270-fitting-water-proof-pg-7-light-grey-csa-bimed-bsr-11.html)
Cable Gland | 9mm | 6 | https://leeselectronic.com/en/product/6125-fitting-water-proof-pg-9-black.html (https://leeselectronic.com/en/product/6125-fitting-water-proof-pg-9-black.html)
Screws/Bolts | 4x1/2”, 6x1/2” | Box

carlon-thermoplastic-junction-box-8x8x4-in/

61270-fitting-water-proof-pg-7-light-grey-csa-bimed-bsr-11.

Table 6: Hardware BOM required for building project

### 9.2 Electronics

### 9.2.1 Sensor Devices

Designator | Description | Quantity | Link
Temperature | DS18B20 | 1 | https://www.digikey.ca/en/products/detail/dfrobot/DFR0198/7597054 (https://www.digikey.ca/en/products/detail/dfrobot/DFR0198/7597054)
Water Level | SEN0204 | 1 | https://www.digikey.ca/en/products/detail/dfrobot/SEN0204/6579443?s=N4IgTCBcDaIMoFEByAGMKAsIC6BfIA (https://www.digikey.ca/en/products/detail/dfrobot/SEN0204/6579443?s=N4IgTCBcDaIMoFEByAGMKAsIC6BfIA)
pH Sensor | SEN0161-V2 | 1 | https://www.digikey.ca/en/products/detail/dfrobot/SEN0161-V2/9608223 (https://www.digikey.ca/en/products/detail/dfrobot/SEN0161-V2/9608223)
Leak Sensor | Analog Leak Sensor | 1 | https://www.amazon.ca/gp/product/B07PV9SYLV/ref=ppx_yo_dt_b_asin_title_o03_s00?ie=UTF8&psc=1 (https://www.amazon.ca/gp/product/B07PV9SYLV/ref=ppx_yo_dt_b_asin_title_o03_s00?ie=UTF8&psc=1)

Table 7: Sensor Bill of Materials

### 9.2.2 Control Devices

Some devices will be necessary to set up the control system aspect. This includes what is seen below in the table BOM. The design currently has 2 unused relay channels that may be used in future expansion.

Designator | Description | Quantity | Link
Relay Mod-ule | 4 Chan-nel 5V controlled Relay Mod-ule | 1 | https://leeselectronic.com/en/product/31302-4-relay-digital-module-5v.html (https://leeselectronic.com/en/product/31302-4-relay-digital-module-5v.html)
Solenoid Valve | 12V 3/4” solenoid for connecting with hoses | 1 | https://leeselectronic.com/en/product/440-44012VSOLENOIDVALVE34SMALLROB104.html (https://leeselectronic.com/en/product/440-44012VSOLENOIDVALVE34SMALLROB104.html)
Peristaltic Pump | 12V Peri-staltic Pump with surgical tubing | 1-2 | https://www.amazon.ca/Peristaltic-Liquid-Dosing-Silicone-Tubing/dp/B075VN1QZM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 (https://www.amazon.ca/Peristaltic-Liquid-Dosing-Silicone-Tubing/dp/B075VN1QZM?hvadid=292901727312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)

Power Supply

12V 2A
Power Supply
1 | https://www.amazon.ca/
Adapter-Supply-Switching-100-240V-Transformer/ dp/B0711SZCMQ/ref=sxin_9_ac_d_rm?ac_ md=2-2-MTJ2IDJhIHBvd2VyIHN1cHBseQ% 3D%3D-ac_d_rm&cv_ct_cx=12V%2Bpower% 2Bsupply&dchild=1&keywords=12V%2Bpower% 2Bsupply&pd_rd_i=B0711SZCMQ&pd_rd_r= 1eff5954-32d8-4e80-8994-f3f9e1651a94& pd_rd_w=vjLDB&pd_rd_wg=riHjN&pf_rd_p= cf70c38a-5522-42af-aeb2-119882942fe1& pf_rd_r=Z0P28K1ZC0Q2NJ9QT85Q& qid=1618245824&sr=
1-3-12d4272d-8adb-4121-8624-135149aa9081&
th=1 (https://www.amazon.ca/Adapter-Supply-Switching-100-240V-Transformer/dp/B0711SZCMQ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) | or | https://www.amazon.ca/
ALITOVE-Universal-Regulated-Switching-Transformer/ dp/B078RY6YY3/ref=sr_1_15?dchild=1& keywords=12V+power+supply&qid=1618245824&
sr=8-15 (https://www.amazon.ca/ALITOVE-Universal-Regulated-Switching-Transformer/dp/B078RY6YY3)
Table 8: Control Devices Bill of Materials

### 9.2.3 Electronic Parts for PCB

Designator | Description | Quantity | Link
12V in | Power 12V in | 1 | https://www.digikey.ca/en/products/detail/on-shore-technology-inc/OSTVN02A150/1588862 (https://www.digikey.ca/en/products/detail/on-shore-technology-inc/OSTVN02A150/1588862)
A1 0, A1 1, A1 2, A1 3 | Header, 3-pin | 4 | https://www.digikey.ca/en/products/detail/on-shore-technology-inc/OSTVN03A150/1588863 (https://www.digikey.ca/en/products/detail/on-shore-technology-inc/OSTVN03A150/1588863)
ADC 0, ADC 1 | Analog to digital converter | 2 | https://www.digikey.ca/en/products/detail/adafruit-industries-llc/1085/5761229 (https://www.digikey.ca/en/products/detail/adafruit-industries-llc/1085/5761229)
Bat | 2AA Bat-tery Holder | 1 | https://www.digikey.ca/en/products/detail/hammond-manufacturing/BH2AAW/3869832 (https://www.digikey.ca/en/products/detail/hammond-manufacturing/BH2AAW/3869832)
Boost 0, Boost 1 | 5V Boost converter | 2 | https://www.pololu.com/product/2562
C1 (4.7uF) | Capacitor | 1 | https://www.digikey.ca/en/products/detail/tdk-corporation/FA20X7S2A475KRU00/7384281 (https://www.digikey.ca/en/products/detail/tdk-corporation/FA20X7S2A475KRU00/7384281)

D1 | Power Schottky rectifier, 60 V, 5 A | 1 | https://www.digikey.ca/en/products/detail/smc-diode-solutions/95SQ015/8021507 (https://www.digikey.ca/en/products/detail/smc-diode-solutions/95SQ015/8021507)
Leak Sensor Header | Header, 3-Pin | 2 | https://www.digikey.ca/en/products/detail/on-shore-technology-inc/OSTVN03A150/1588863 (https://www.digikey.ca/en/products/detail/on-shore-technology-inc/OSTVN03A150/1588863)
Header 20X2 | GPIO shield for RPi | 1 | https://www.digikey.ca/en/products/detail/adafruit-industries-llc/2223/5629433 (https://www.digikey.ca/en/products/detail/adafruit-industries-llc/2223/5629433)
pH Sensor Header | Header, 4-Pin | 1 | https://www.digikey.ca/en/products/detail/on-shore-technology-inc/OSTVN04A150/1588864 (https://www.digikey.ca/en/products/detail/on-shore-technology-inc/OSTVN04A150/1588864)
Q1 | 2N3904 NPN Gen-eral Purpose Amplifier | 1 | https://www.digikey.ca/en/products/detail/stmicroelectronics/2N3904/603420 (https://www.digikey.ca/en/products/detail/stmicroelectronics/2N3904/603420)
R1(10k), R2(1k), R3(220), R4(900k), R5(4.7k), R6(10k), R7(3.9k) | Resistor | 6
Relay header | Relay Con-trol | 1 | https://www.digikey.ca/en/products/detail/on-shore-technology-inc/OSTVN04A150/1588864 (https://www.digikey.ca/en/products/detail/on-shore-technology-inc/OSTVN04A150/1588864)
RPi Vin | Header, 2-pin | 1 | https://www.digikey.ca/en/products/detail/on-shore-technology-inc/OSTVN02A150/1588862 (https://www.digikey.ca/en/products/detail/on-shore-technology-inc/OSTVN02A150/1588862)
Temp Sen-sor header | Header, 3-Pin | 1 | https://www.digikey.ca/en/products/detail/on-shore-technology-inc/OSTVN03A150/1588863 (https://www.digikey.ca/en/products/detail/on-shore-technology-inc/OSTVN03A150/1588863)
V1, V2 | Header, 2-Pin | 2 | https://www.digikey.ca/en/products/detail/on-shore-technology-inc/OSTVN02A150/1588862 (https://www.digikey.ca/en/products/detail/on-shore-technology-inc/OSTVN02A150/1588862)
VR1, VR2 | Voltage Regulator | 2 | https://www.digikey.ca/en/products/detail/texas-instruments/LM7805SX-NOPB/6110585 (https://www.digikey.ca/en/products/detail/texas-instruments/LM7805SX-NOPB/6110585)
WL Sensor Header | Header, 3-Pin | 1 | https://www.digikey.ca/en/products/detail/on-shore-technology-inc/OSTVN03A150/1588863 (https://www.digikey.ca/en/products/detail/on-shore-technology-inc/OSTVN03A150/1588863)

Table 9: PCB Bill of Materials

## References

[1] J. B. Jones, “Hydroponics: a practical guide for the soilless grower.” Boca Raton: CRC Press, 2005.
[2] W. Lennard and S. Goddek, “Aquaponics: The Basics,” Aquaponics Food Production Systems, pp. 113–143, 2019.
[3] Raspberry Pi Zero W.
https://www.raspberrypi.org/products/raspberry-pi-zero-w/?resellerType=home (https://www.raspberrypi.org/products/raspberry-pi-zero-w/?resellerType=home)
[4] “HTTP vs. MQTT: A tale of two IoT protocols,” Google. [Online]. Available: https://cloud.google.com/blog/products/iot-devices/http-vs-mqtt-a-taleof-two-iot-protocols. [Accessed: 13-Apr-2021].
[5] “Choose a Database: Cloud Firestore or Realtime Database — Firebase,” Google. [Online]. Available: https://firebase.google.com/docs/database/rtdbvs-firestore. [Accessed: 13-Apr-2021].
[6] “Get realtime updates with Cloud Firestore — Firebase,” Google. [Online]. Available: https://firebase.google.com/docs/firestore/query-data/listen. [Accessed: 13-Apr-2021].
[7] David Sayson. Aquaponics Expert. Personal Communications. [Date: 25-Sep-2020]

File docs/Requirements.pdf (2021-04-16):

# IoT Monitoring of Aquaponic and

# Hydroponic Food Production

# Requirements

### UBC Electrical and Computer Engineering Capstone 121

Carson Berry

Lynes Chan

Mason Duan

Jayden Leong

Hannah Xu

for

Bernhard Nimmervoll, UBC Mechanical Engineering

UBC SEEDS Sustainability Program

### April 13, 2021

## Revision History

Date | Author | Sections | Change
2020-10-05 | JL | 1.0 - 2.0 | Creation of document skeleton
2020-10-30 | CB | 1.0 - 5.0 | Added system overview and skeleton of subsystem sections
2020-10-30 | CB | 1.0 - 5.0 | Edited Document with feedback from Dr. Lusina and Clients
2020-11-28 | JL | 1.0 - 5.0 | Major revisions to all sections for design review 1.
2021-01-15 | MD | 1.0 - 5.0 | Major revisions to all sections for design review 2.
2021-02-19 | JL | 4.1, 4.2 | Increase specificity and measurability of functional and non-functional requirements. Included NFx and Fx labels for clarity, instead of numbered lists

## Contents

1 Context | 3
2 Domain | 6
3 Goal | 7
4 Requirements | 8
5 Constraints | 9

## 1 Context

In this section, an introduction of our clients and their goals is given. Our clients are Bernhard Nimmervoll of the University of British Columbia (UBC) Mechanical Engineering Department, and Nelly Leo of the UBC Social Ecological Economic Development Studies (SEEDS) Program.

Secondly, this section includes a description of aquaponics and hydroponics. Briefly, aquaponics and hydroponics are food production methods known for being more sustainable than traditional food productions practices.

Finally, a description of the problem this project aims to solve will be given. Overall, this project aims to make aquaponics and hydroponics easier to maintain and monitor. This will, in turn, serve to promote aquaponics and hydroponics as sustainable methods of food production.

### 1.1 Client Introduction

The primary client of this project is Bernhard Nimmervoll, a Technician for the UBC Mechanical Engineering Department. Bernhard is a passionate advocate of sustainabililty initiatives, including being a hobbyist aquaponics grower in his spare time. Bernhard introduced this project as a way to promote aquaponics and hydroponics as sustainable food production methods, and as a way to combat food insecurity.

Bernhard has partnered with a UBC organization called the Social Ecological Economic Development Studies (SEEDS) Sustainability program. The SEEDS program developed out of UBC’s commitment to being a global leader in integrated sustainability [1]. As such, SEEDS is an organization whose aims are to advance the wellbeing of the environment, local biodiversity, food systems, responsible consumption and community inclusion. They are pursuing these aims by supporting student-led research and development about climate friendly food systems, urban food production for community resilience, biodiverse food systems, zero-waste, and food justice and sovereignty. This project is one of many such UBC SEEDS projects.

UBC SEEDS’ has five main research goals, which are shown in Figure 1. The research goal, ‘Enable the great food transformation’, is the primary focus of our project. This goal is typically pursued by researching food security and sustainability, implementing policies and plans, and participating in education, engagement, and demonstration. In our case, our project will contribute to this goal by advancing technology related to sustainable food growth using aquaponics and hydroponics.

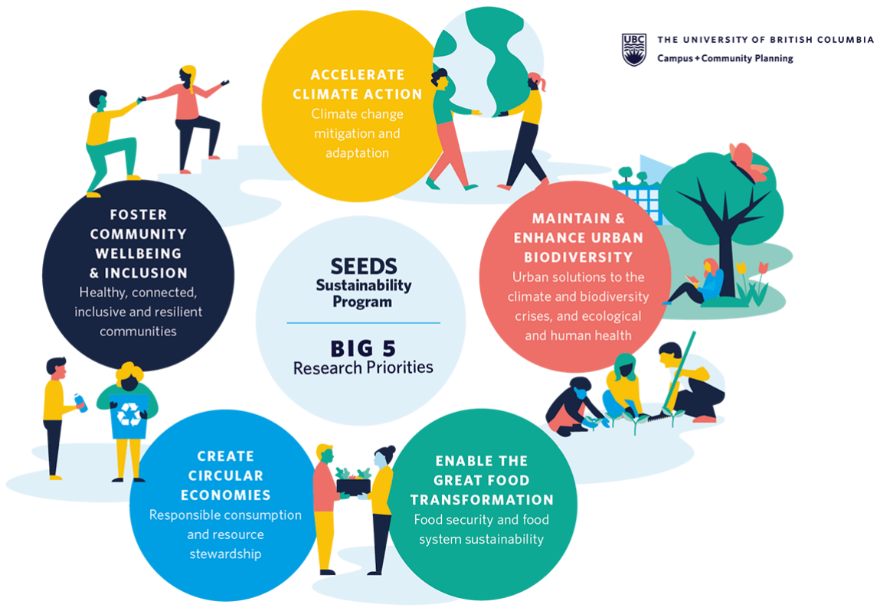
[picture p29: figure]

Figure 1: UBC SEEDS big five research priorities [2]

Nelly Leo is the UBC SEEDS coordinator overseeing this project. She is responsible for ensuring that this project meets overall SEEDS objectives.

### 1.2 Hydroponics and Aquaponics

Hydroponics is a method of agriculture where plants are grown in a nutrient-rich aqueous solution. Nutrients in hydroponics are inputted by the grower to nourish plants. This contrasts traditional forms of agriculture, where plants are grown in soil.

Aquaponics is very similar to hydroponics. In aquaponics, plants are also grown in an aqueous solution, however plants recieve nutrients in a different manner. Instead of growers inputting nutrients, plants recieve nutrients from fish waste. To make this possible, fish are raised in water tanks that the plants are grown in. Aquaponics recieves its name because of this, by being a mixture of aquaculture and hydroponics. A simplified diagram of aquaponics is show in Figure 2.


Figure 2: A diagram of a basic aquaponics system

Both hydroponics and aquaponics are being developed as more sustainable approaches to agriculture than traditional methods for the following reasons [3]:

1. Higher crop production per unit area;
2. Faster plant growth;
3. Lower water usage;
4. Lower susceptibility to pests if grown indoors.

For aquaponics, there are also the following additional benefits [4][5]:

1. Fish and plants form a circular, self-sustaining ecosystem;
2. Fish food is the only input needed;
3. Fish as well as plants can be harvested for food.

For the benefits listed above, our clients, Bernhard Nimmervoll and UBC SEEDS, are interested in improving and advocating for these more sustainable agricultural methods.

### 1.3 Problem

Both aquaponic and hydroponic systems need to be carefully monitored. Plants require that the aqueous solutions they are planted in have all neccesary nutrients. They also require other environmental variables to be monitored, including solution pH, light intensity, humidity, and more. In addition, aquaponic systems are even more difficult systems to maintain due to their complex multi-species dynamics. Systems need to be balanced such that fish, bacteria, and plants can all thrive.

With this system complexity, hydroponics and aquaponics require frequent supervision and maintenance by a knowledgeable operator. This adds significant cost and labor for aquaponics and hydroponics growers. This can be discouraging for small scale and hobbyist aquaponic or growers who do not currently have access to an affordable, automated monitoring and control system.

## 2 Domain

This project is within the domain of aquaponics and hydroponics monitoring and control systems typically built by hobbyists and small companies. These are small-scale monitoring and control systems usually designed for and installed on a single aquaponics or hydroponics system. They are also usually open-source and nonproprietary. The vast majority of these systems monitor their systems using internet connectivity, making them categorizable as small-scale internet of things (IoT) projects.

Many of the previous implementations of systems of this type are simplistic and designed for single systems without much forethought for future development [7][8]. Some of the systems have been designed with future improvements, ease of setup, cost, and efficiency in mind [9][10]. An example of such a system is shown below in Figure 3. This system is quite expensive for an monitoring system that is built using off the self components, costing around $850. The system also seems to have limited external monitoring capabilities and no licensing for open source although they claim to be an open source project. As well, the monitoring system doesn’t record any data and does not seem to have any response system in place in case of power failure.


Figure 3: An example of an existing system called HydroBot [10]

## 3 Goal

The goal of this project is to develop a user-friendly, no-technical-expertise-needed solution for monitoring and control of hydroponic or aquaponic systems. This system should utilize open-source and low cost technologies wherever possible to minimize barriers to replication and access. In terms of scope, our project serves to deliver a working prototype of such a system which is installed on an existing hydroponic or aquaponic system.

When completed, this project will help solve the problem of hobbyist and aquaponic growers monitoring and maintaining their systems. It will help reduce cost, time, and effort associated with aquaponics and hydroponic systems; and help reduce system failures resulting in production losses.

In addition to these benefits, this project will also contribute towards larger goals including increasing food systems sustainability, reducing food insecurity, and increasing sustainability awareness. First of all, by making hydroponics and aquaponics systems easier to develop and maintain, this may encourage more growers to use these methods. This, in turn, can promote food systems sustainabililty as aquaponics and hydroponics have advantages over traditional growing methods.

In terms of food insecurity, this project may be included in future on-campus aquaponics or hydroponics growing systems. For example, a physical ‘FoodHub’ is being envisioned UBC Okanagan (UBCO) campus [6]. This ‘FoodHub’ may provide affordable, local, organic vegetables and fish to UBCO community members as an effort to reduce student food insecurity. This Food Hub is being planned to include an aquaponic system of both functional, research, and educational value. The product of this project could be a helpful addition to monitor such a system, and could therefore contribute to broader issues including reducing food insecurity.

## 4 Requirements

In order to meet the goals in section 3, our team has generated functional and non-functional requirements for this project.

### 4.1 Functional Requirements

This project must perform the following functions:

F1 Display measurements of critical system variables in hydroponic or aquaponic systems. For the scope of our project, critical system variables include and are limited to pH, water level, water leakage, and water temperature. All displayed measurements must be updated at a minimum of every five minutes.

F2 Store and display past measurements of critical system variables so hydroponic or aquaponic growers can analyze system trends. The system must be capable of storing and displaying at least the past 3 months worth of measurements.

F3 Send alerts to growers within 1 minute of a detecting that a critical system variable is outside of a normal range. Growers will specify normal ranges for each of the critical system variables.

F4 Adjust pH level and water level automatically such that they always stay within a pre-defined range. This pre-defined range for pH and water level can be configured by growers depending on the needs of their hydroponic or aquaponic system.

F5 Operate for at least 8 hours in the event of a power supply failure or outage. The system must also send an alert to growers indicating that there was a power failure. Alerts should occur a 1 minute of the power failure.

F6 Give growers the ability re-calibrate sensors and actuators. These re-calibrations can be made at any time.

### 4.2 Non-Functional Requirements

The following is a list of non-functional requirements for this project. This project must:

NF1 Cost less than $300 CAD per system. Additional monthly servicing fees of must also be less than $5 per month.

NF2 Be designed to work with any small-scale aquaponics or hydroponics systems. For this project, small-scale aquaponics or hydroponic systems have under 200 plants and under 3000 gallons of water.

NF3 Ensure that only permitted growers can monitor and control hydroponic or aquaponic systems. Future administrators of our project must enable growers to monitor and control a given hydroponic or aquaponic system. Otherwise, access to monitor a given hydroponic or aquaponic system will not be permitted.

NF4 Be water resistant. An IP rating of IP67 (Protected from immersion between 15 centimeters and 1 meter in depth) must be satisfied.

NF5 Be able to monitor different or additional aquaponics or hydroponics system variables, depending on the grower’s preference.

NF6 Measure all critical system variables within an accuracy of 5%.

NF7 Maintain all controlled variables within an accuracy of 10%.

## 5 Constraints

The following is a list of constraints on our design:

C1 All software developed must be open-source, with appropriate licensing to allow for legal modification, duplication, and sharing. The license we have chosen is the GNU General Public License v3.0 as it allows the community to make changes and to use the code for personal purposes but prevents distributing closed source versions.

## References

[1] UBC Strategic Plan - Shaping UBC’s Next Century. 2018. https://strategicplan.ubc.ca/wp-content/uploads/2019/09/2018_UBC_Strategic_Plan_Full-20180425.pdf (https://strategicplan.ubc.ca/wp-content/uploads/2019/09/2018_UBC_Strategic_Plan_Full-20180425.pdf)
[2] SEEDS Sustainability Students. 2020. https://sustain.ubc.ca/teaching-applied-learning/seeds-sustainability-program/seeds-sustainability-students (https://sustain.ubc.ca/teaching-applied-learning/seeds-sustainability-program/seeds-sustainability-students)
[3] Hydroponics vs. Aquaponics - A Complete, and Honest Comparison. 2019. https://www.trees.com/gardening-and-landscaping/hydroponics-vs-aquaponics (https://www.trees.com/gardening-and-landscaping/hydroponics-vs-aquaponics)
[4] What Are The Benefits of Aquaponics? Organic Farming and More Benefits.
2019.
https://gogreenaquaponics.com/blogs/news/what-are-the-benefits-of-aquaponics
[5] Why Aquaponics?
https://stuppy.com/aquaponics/aquaponiclearn/why-aquaponics/
[6] Envisioning a Physical Food Hub at UBCO. 2020. https://sustain.ubc.ca/about/resources/envisioning-physical-food-hub-ubco
[7] AMACS Aquaponics Monitoring And Control System. 2017. https://www.hackster.io/locogenii/amacs-aquaponics-monitoring-and-control-system-3c0165
[8] IoT NFT Aquaponic System Controler With WebApp https://www.instructables.com/IoT-NFT-Aquaponic-System-Controler-with-WebApp-Int/
[9] Open Aquarium
https://www.cooking-hacks.com/documentation/tutorials/open-aquarium-aquaponics-fish-tank-monitoring-arduino.html (https://www.cooking-hacks.com/documentation/tutorials/open-aquarium-aquaponics-fish-tank-monitoring-arduino.html)
[10] Hydro.Bot. 2020.
https://hydro.bot/

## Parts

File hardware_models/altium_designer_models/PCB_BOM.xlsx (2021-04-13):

Comment | Description | Designator | Footprint | Value | Quantity | Link
Header 2 | Power 12V in | 12V_in | 2_channel_terminal_black |  | 1 | https://www.digikey.ca/en/products/detail/on-shore-technology-inc/OSTVN02A150/1588862
 | V0+ -, V1+ - |  | 2_channel_terminal_black |  | 2 | https://www.digikey.ca/en/products/detail/on-shore-technology-inc/OSTVN02A150/1588862
 | Rpi Vin |  | 2_channel_terminal_black |  | 1 | https://www.digikey.ca/en/products/detail/on-shore-technology-inc/OSTVN02A150/1588862

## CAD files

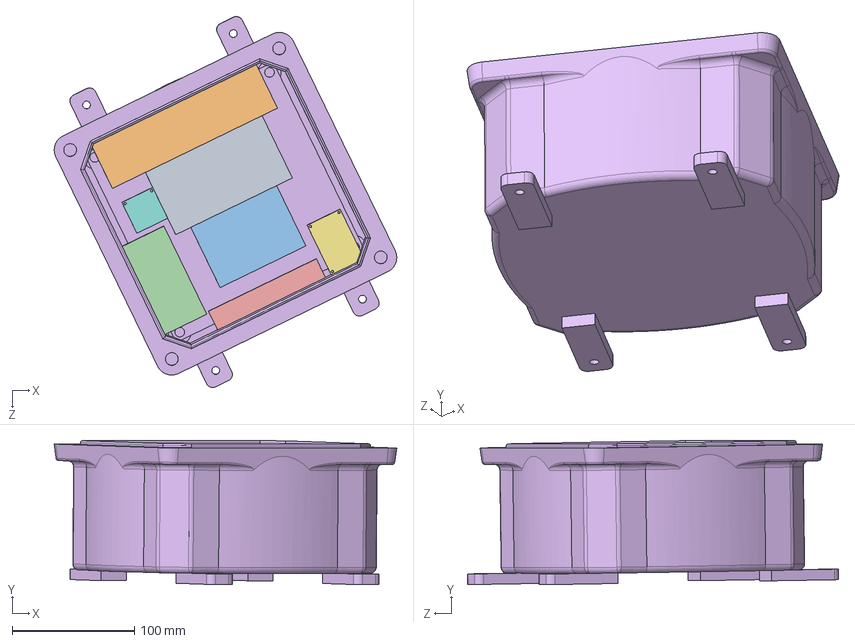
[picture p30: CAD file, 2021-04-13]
hardware_models/solidworks2019_models/Piponics_enlcosure.SLDASM
280.0 x 117.9 x 303.1 mm
breadboard
Power_supply
relay_block
RPi_case
Terminal_block_metal
5376K132_WATERTIGHT ENCLOSURE WITH VERSA-MOUNT SYSTEM
pH_board
water_level_sensor_board

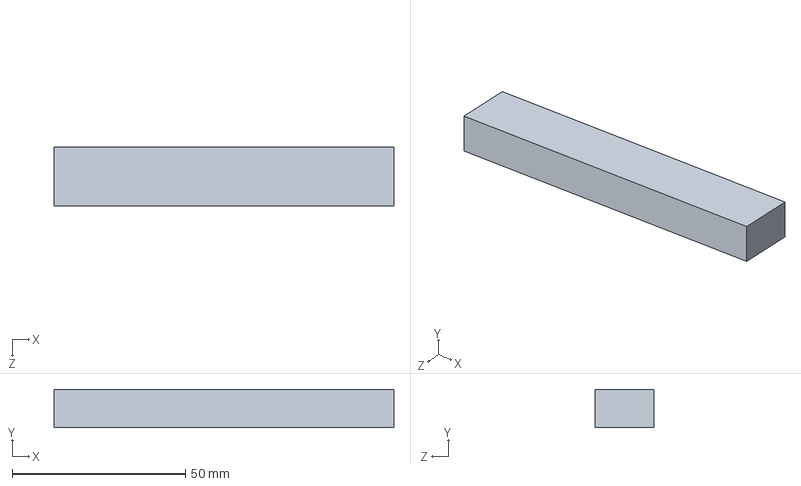
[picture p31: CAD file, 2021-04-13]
hardware_models/solidworks2019_models/Terminal_block_metal.SLDPRT
98.0 x 11.0 x 17.0 mm

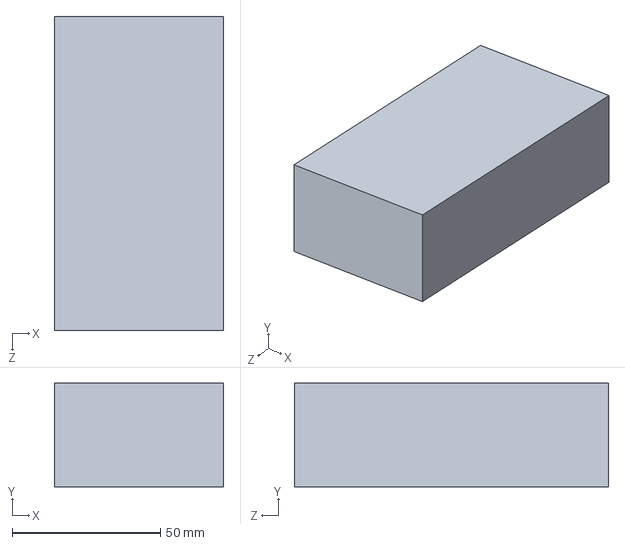
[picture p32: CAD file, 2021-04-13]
hardware_models/solidworks2019_models/breadboard.SLDPRT
57.0 x 35.0 x 106.0 mm

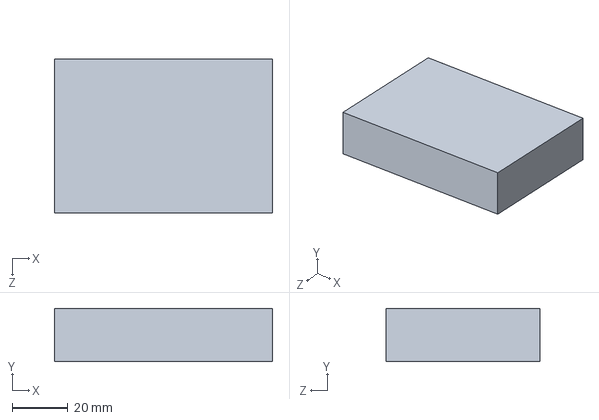
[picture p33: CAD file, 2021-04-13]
hardware_models/solidworks2019_models/relay_block.SLDPRT
78.0 x 19.0 x 55.0 mm

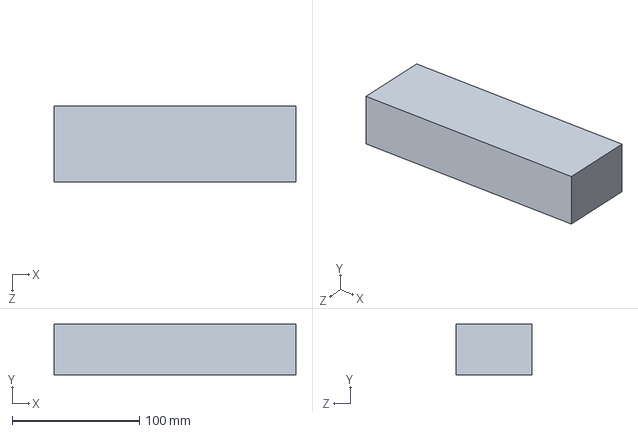
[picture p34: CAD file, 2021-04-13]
hardware_models/solidworks2019_models/Power_supply.SLDPRT
190.0 x 40.0 x 60.0 mm

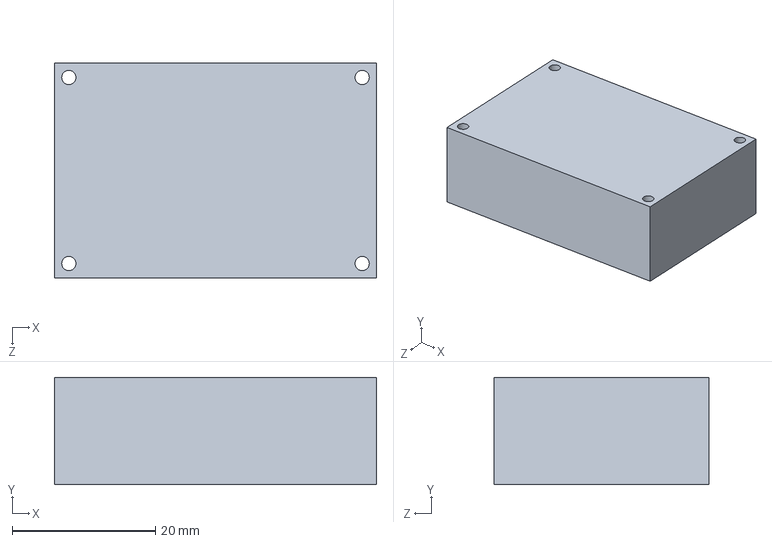
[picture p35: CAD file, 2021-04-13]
hardware_models/solidworks2019_models/pH_board.SLDPRT
45.0 x 15.0 x 30.0 mm

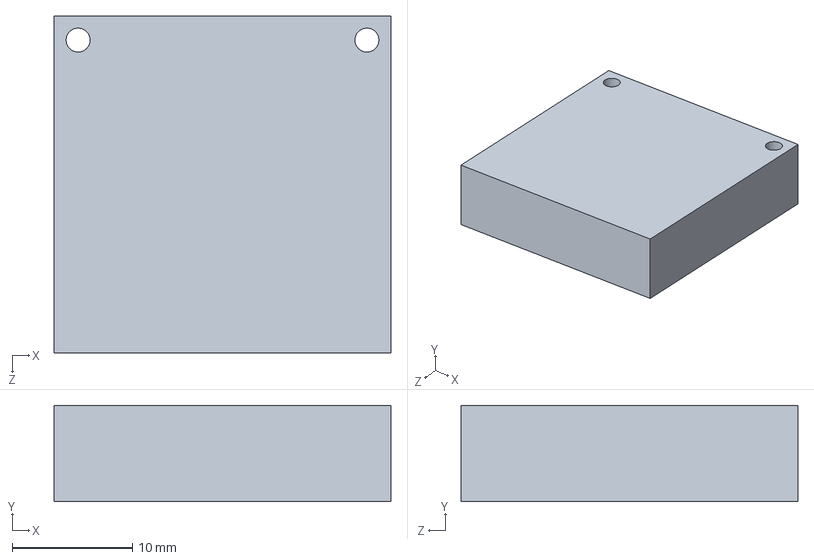
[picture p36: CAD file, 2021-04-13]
hardware_models/solidworks2019_models/water_level_sensor_board.SLDPRT
28.0 x 8.00 x 28.0 mm

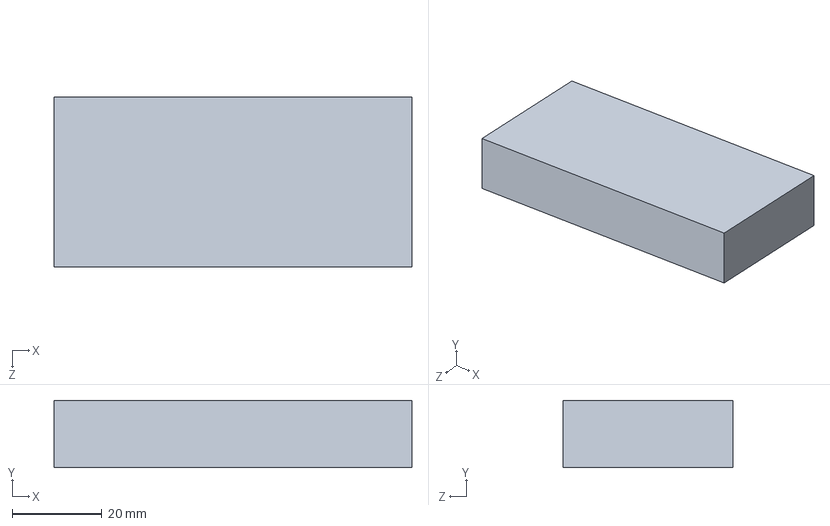
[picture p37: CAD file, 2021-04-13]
hardware_models/solidworks2019_models/RPi_case.SLDPRT
80.0 x 15.0 x 38.0 mm

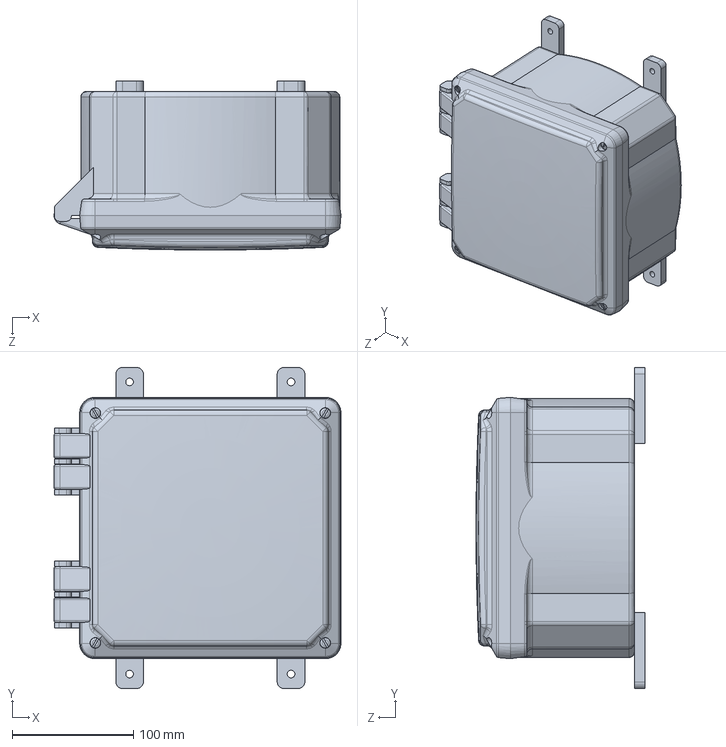
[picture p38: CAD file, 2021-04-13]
hardware_models/solidworks2019_models/5376K132_WATERTIGHT ENCLOSURE WITH VERSA-MOUNT SYSTEM.SLDPRT
237.1 x 265.2 x 139.7 mm

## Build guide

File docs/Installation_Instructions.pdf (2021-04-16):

# IoT Monitoring of Aquaponic and

# Hydroponic Food Production

# Installation and Setup Instructions

### UBC Electrical and Computer Engineering Capstone 121

Carson Berry

Lynes Chan

Mason Duan

Jayden Leong

Hannah Xu

for

UBC SEEDS Sustainability Program

Bernhard Nimmervoll, UBC Mechanical Engineering

### April 12, 2021

## Contents

1 Introduction | 4
2 Equipment Requirements | 4
3 Electronic Circuit Manufacturing | 4
4 Sensors | 9

5 Hardware Setup | 14
6 Software Setup | 16

### 0.1 Change Log

The change log documents changes made to the document.

Table 1: Change Log of Document
Date | Author | Sections | Change
2021-01-23 | CB | 1.0 - 4.0 | Creation of document skeleton
2021-04-04 | CB | 1.0 - 5.0 | Added Electronic, Hardware manufacturing steps
2021-04-08 | LC | 6.1-6.2 | Fixed formatting, Edited Raspberry Pi setup, added Installing the Project

## 1 Introduction

This suite of setup instructions is designed to walk a person with some familiarity of

circuits, CAD tools, and programming through the steps of setting up a monitoring

and control system for their pre-existing aquaponic or hydroponic growing system.

The setup and manufacturing of this system can divided into several steps.

1. Electronic Circuit manufacturing
2. Mechanical component preparation
3. Integration and Assembly

## 2 Equipment Requirements

Some tools will be required for the assembly of this system. They may be seen

below.

1. Screw-Driver, multi-tool
2. Adjustable Wrench
3. Soldering Iron
4. Solder, flux, and Solder paste
5. Hand-Saw
6. Power-Drill

## 3 Electronic Circuit Manufacturing

### 3.1 Printed Circuit Board

This project includes the design for a printed circuit board (PCB). This PCB is

designed to be a ”hat” for the Raspberry Pi. That is, it will sit directly on the header pins of the Raspberry Pi.

### 3.1.1 Ordering the PCB

The PCB will need to be ordered from a PCB manufacturing service. Several options

are shown below. Each service may require a different combination of files, so please

check in with their requirements.

Local PCB Manufacturers:

1. Canadian Circuits Inc., http://www.canadiancircuits.com/
2. Enigma Interconnect, https://www.enigmacorp.com/
3. Omni Circuit Boards, https://www.omnicircuitboards.com/

Local Vancouver, BC assembly services:

1. Active Electronic Manufacturing, http://activeelectronic.com/
2. Leading Edge Manufacturing, http://www.leadingedge-mfg.com/

Foreign PCB manufacturing / Assembly:

1. Advanced Circuits 4PCB (PCB & Assembly), https://www.4pcb.com/
2. JLCPCB (PCB & Assembly), https://jlcpcb.com/
3. MyRo PCB (PCB & Assembly), http://www.myropcb.com/
4. Osh Stencils, https://www.oshstencils.com/
5. PCB Cart (PCB & Assembly), https://www.pcbcart.com/
6. PCB Way (PCB & Assembly), https://www.pcbway.com/
7. SpeedyPCB (PCB), http://www.speedypcb.com/

### 3.1.2 Ordering components for the PCB

This PCB will act as the interface between sensors, sensor break-out boards, relays,

and the Raspberry Pi.

For a complete listing of the components needed to populate the PCB please refer

to table 2 below.

Designator | Description | Quantity | Link
12V in | Power 12V in | 1 | https://www.digikey.ca/en/products/detail/on-shore-technology-inc/OSTVN02A150/1588862 (https://www.digikey.ca/en/products/detail/on-shore-technology-inc/OSTVN02A150/1588862)
A1 0, A1 1, A1 2, A1 3 | Header, 3-pin | 4 | https://www.digikey.ca/en/products/detail/on-shore-technology-inc/OSTVN03A150/1588863 (https://www.digikey.ca/en/products/detail/on-shore-technology-inc/OSTVN03A150/1588863)
ADC 0, ADC 1 | Analog to digital converter | 2 | https://www.digikey.ca/en/products/detail/adafruit-industries-llc/1085/5761229 (https://www.digikey.ca/en/products/detail/adafruit-industries-llc/1085/5761229)
Bat | 2AA Bat-tery Holder | 1 | https://www.digikey.ca/en/products/detail/hammond-manufacturing/BH2AAW/3869832 (https://www.digikey.ca/en/products/detail/hammond-manufacturing/BH2AAW/3869832)
Boost 0, Boost 1 | 5V Boost converter | 2 | https://www.pololu.com/product/2562
C1 (4.7uF) | Capacitor | 1 | https://www.digikey.ca/en/products/detail/tdk-corporation/FA20X7S2A475KRU00/7384281 (https://www.digikey.ca/en/products/detail/tdk-corporation/FA20X7S2A475KRU00/7384281)
D1 | Power Schottky rectifier, 60 V, 5 A | 1 | https://www.digikey.ca/en/products/detail/smc-diode-solutions/95SQ015/8021507 (https://www.digikey.ca/en/products/detail/smc-diode-solutions/95SQ015/8021507)
Leak Sensor Header | Header, 3-Pin | 2 | https://www.digikey.ca/en/products/detail/on-shore-technology-inc/OSTVN03A150/1588863 (https://www.digikey.ca/en/products/detail/on-shore-technology-inc/OSTVN03A150/1588863)
Header 20X2 | GPIO shield for RPi | 1 | https://www.digikey.ca/en/products/detail/adafruit-industries-llc/2223/5629433 (https://www.digikey.ca/en/products/detail/adafruit-industries-llc/2223/5629433)

pH Sensor Header | Header, 4-Pin | 1 | https://www.digikey.ca/en/products/detail/on-shore-technology-inc/OSTVN04A150/1588864 (https://www.digikey.ca/en/products/detail/on-shore-technology-inc/OSTVN04A150/1588864)
Q1 | 2N3904 NPN Gen-eral Purpose Amplifier | 1 | https://www.digikey.ca/en/products/detail/stmicroelectronics/2N3904/603420 (https://www.digikey.ca/en/products/detail/stmicroelectronics/2N3904/603420)
R1(10k), R2(1k), R3(220), R4(900k), R5(4.7k), R6(10k), R7(3.9k) | Resistor | 6
Relay header | Relay Con-trol | 1 | https://www.digikey.ca/en/products/detail/on-shore-technology-inc/OSTVN04A150/1588864 (https://www.digikey.ca/en/products/detail/on-shore-technology-inc/OSTVN04A150/1588864)
RPi Vin | Header, 2-pin | 1 | https://www.digikey.ca/en/products/detail/on-shore-technology-inc/OSTVN02A150/1588862 (https://www.digikey.ca/en/products/detail/on-shore-technology-inc/OSTVN02A150/1588862)
Temp Sen-sor header | Header, 3-Pin | 1 | https://www.digikey.ca/en/products/detail/on-shore-technology-inc/OSTVN03A150/1588863 (https://www.digikey.ca/en/products/detail/on-shore-technology-inc/OSTVN03A150/1588863)
V1, V2 | Header, 2-Pin | 2 | https://www.digikey.ca/en/products/detail/on-shore-technology-inc/OSTVN02A150/1588862 (https://www.digikey.ca/en/products/detail/on-shore-technology-inc/OSTVN02A150/1588862)
VR1, VR2 | Voltage Regulator | 2 | https://www.digikey.ca/en/products/detail/texas-instruments/LM7805SX-NOPB/6110585 (https://www.digikey.ca/en/products/detail/texas-instruments/LM7805SX-NOPB/6110585)
WL Sensor Header | Header, 3-Pin | 1 | https://www.digikey.ca/en/products/detail/on-shore-technology-inc/OSTVN03A150/1588863 (https://www.digikey.ca/en/products/detail/on-shore-technology-inc/OSTVN03A150/1588863)

Table 2: PCB Bill of Materials

To automatically purchase the required components from digikey.ca please find a

shopping cart at this url: https://www.digikey.ca/short/tqvrt484. If there

is any problem with that digital cart, please try uploading the saved spreadsheet

piponic BOM digikey cart.xlxs to the website. One note is that the resistors saved in

this cart are not special, but were the cheapest available options in single quantities.

We recommend investing in a resistor kit, but will leave that decision to the grower.

This cart does not contain everything needed to purchase the parts for this project.

Some items must be purchased from other websites, such as the Polulu boost con-

verters. The sensors are also not included in the above table.

### 3.1.3 Soldering

Once all the components have been purchased, and the PCB has been received from

manufacturers it must be soldered together. This should be done in a well-ventilated

workspace to avoid aspiration of noxious fumes.

Some of the components belong on the top of the PCB, and some on the bottom. The

voltage regulators, resistors, diode, capacitor, and the analog to digital converters

all belong on the bottom. In addition the header-pin for the raspberry pi should be placed with the female side on the bottom (so that the male-ends are exposed on

the top side).

The most challenging component to solder on the board will likely be the voltage

regulators, which are in a surface-mount package. Despite this challenge, they can

still be soldered with a conventional soldering iron. When doing so, set the soldering

iron to 230 C, and take care that it is fully heated before beginning. Apply solder-

paste in an even layer to the exposed VR1 and VR2 footprints. Place the voltage

regulators on top of the paste, and heat up the exposed leads with the iron. Try to

keep the heating under 10s to avoid damaging the device.

The rest of the through-hole components can be soldered normally using solder-wire.

Once finished soldering all of the components, clean the board with a cotton swab

soaked in rubbing alcohol to ensure best performance.

## 4 Sensors

### 4.1 Sensor Bill of Materials

The base array of sensors that are recommended can be seen in the table below.

Designator | Description | Quantity | Link
Temperature | DS18B20 | 1 | https://www.digikey.ca/en/products/detail/dfrobot/DFR0198/7597054 (https://www.digikey.ca/en/products/detail/dfrobot/DFR0198/7597054)
Water Level | SEN0204 | 1 | https://www.digikey.ca/en/products/detail/dfrobot/SEN0204/6579443?s=N4IgTCBcDaIMoFEByAGMKAsIC6BfIA (https://www.digikey.ca/en/products/detail/dfrobot/SEN0204/6579443?s=N4IgTCBcDaIMoFEByAGMKAsIC6BfIA)
pH Sensor | SEN0161-V2 | 1 | https://www.digikey.ca/en/products/detail/dfrobot/SEN0161-V2/9608223 (https://www.digikey.ca/en/products/detail/dfrobot/SEN0161-V2/9608223)
Leak Sensor | Analog Leak Sensor | 1 | https://www.amazon.ca/gp/product/B07PV9SYLV/ref=ppx_yo_dt_b_asin_title_o03_s00?ie=UTF8&psc=1 (https://www.amazon.ca/gp/product/B07PV9SYLV/ref=ppx_yo_dt_b_asin_title_o03_s00?ie=UTF8&psc=1)

Table 3: Sensor Bill of Materials

### 4.2 Control Devices Bill of Materials

Some devices will be necessary to set up the control system aspect. This includes

what is seen below in the table BOM. The design currently has 2 unused relay

channels that may be used in future expansion.

Designator | Description | Quantity | Link
Relay Mod-ule | 4 Chan-nel 5V controlled Relay Mod-ule | 1 | https://leeselectronic.com/en/product/31302-4-relay-digital-module-5v.html (https://leeselectronic.com/en/product/31302-4-relay-digital-module-5v.html)

Solenoid Valve | 12V 3/4” solenoid for connecting with hoses | 1 | https://leeselectronic.com/en/product/440-44012VSOLENOIDVALVE34SMALLROB104.html (https://leeselectronic.com/en/product/440-44012VSOLENOIDVALVE34SMALLROB104.html)
Peristaltic Pump | 12V Peri-staltic Pump with surgical tubing | 1-2 | https://www.amazon.ca/Peristaltic-Liquid-Dosing-Silicone-Tubing/dp/B075VN1QZM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 (https://www.amazon.ca/Peristaltic-Liquid-Dosing-Silicone-Tubing/dp/B075VN1QZM?hvadid=292901727312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)

Power Sup-

ply

12V 2A

Power Sup-

ply

1 | https://www.amazon.ca/

Adapter-Supply-Switching-100-240V-Transformer/

dp/B0711SZCMQ/ref=sxin_9_ac_d_rm?ac_

md=2-2-MTJ2IDJhIHBvd2VyIHN1cHBseQ%

3D%3D-ac_d_rm&cv_ct_cx=12V%2Bpower%

2Bsupply&dchild=1&keywords=12V%2Bpower%

2Bsupply&pd_rd_i=B0711SZCMQ&pd_rd_r=

1eff5954-32d8-4e80-8994-f3f9e1651a94&

pd_rd_w=vjLDB&pd_rd_wg=riHjN&pf_rd_p=

cf70c38a-5522-42af-aeb2-119882942fe1&

pf_rd_r=Z0P28K1ZC0Q2NJ9QT85Q&

qid=1618245824&sr=

1-3-12d4272d-8adb-4121-8624-135149aa9081&

th=1 (https://www.amazon.ca/Adapter-Supply-Switching-100-240V-Transformer/dp/B0711SZCMQ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) | or | https://www.amazon.ca/

ALITOVE-Universal-Regulated-Switching-Transformer/

dp/B078RY6YY3/ref=sr_1_15?dchild=1&

keywords=12V+power+supply&qid=1618245824&

sr=8-15 (https://www.amazon.ca/ALITOVE-Universal-Regulated-Switching-Transformer/dp/B078RY6YY3)
Table 4: Control Devices Bill of Materials

### 4.3 Sensor Placement in Aquaponic or Hydroponic system

The sensors should be placed in location with water flow and minimal contaminating

waste deposits. The pH sensor should be placed in the water, upstream of the

peristaltic pump’s effluent hose.

The temperature sensor can be placed anywhere in the water.

The leak sensor(s) should be placed out of the water wherever you don’t want water

to pool.

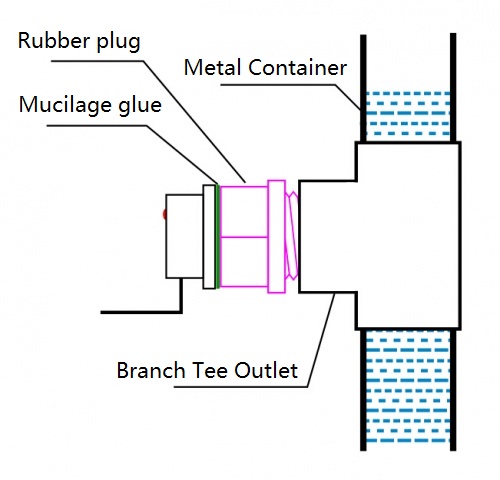
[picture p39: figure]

Figure 1: Metal Enclosure Water Level Sensor installation.

The water level sensor should be attached to the outside of the tank (if the tank

is plastic) at the line where you want the minimum water level to be. It should

be attached with glue or tape to a plastic wall. If your water tank is metallic, the

water level sensor will provide false readings, so a plastic covering for the water level

sensor should be added as seen in figure 1.

### 4.4 Enclosure Location

The main enclosure needs to be located close to a power-outlet. An extension cord

could be used to extend the range of permissible locations. The main enclosure

should also be located close to the aquaponic or hydroponic system so that all

sensors can adequately reach. The wire length of the sensors can be adjusted for

this.

### 4.5 Wiring

A braided, multiconductor wire is recommended to interface between the sensor

break-out boards and the sensors. This wire will be clamped down with cable

glands as it passes through holes drilled in the enclosure wall.


Figure 2: Waterproof Nylon Cable Gland example.

The wall-outlet power cord will also pass through the enclosure wall in this manner.

### 4.5.1 Cable Length

The cable length can selected based on your aquaponic or hydroponic system setup.

That is, measure where you will be mounting the main enclosure, and where you

want the sensors to be.

### 4.6 Temperature Sensor

The DS18B20 temperature sensor must be wired up correctly to the raspberry pi.

This sensor utilizes the one-wire interface protocol. This is accomplished by con-

necting the red 5 V wire to pin 4, the black ground wire to Pin 6, and the orange

data wire to pin 7. A 4.7 Ω resistor should be included between the data pin and

5V, acting as a pull-up resistor.

The one wire interface protocol should be enabled using the sudoraspi − conf ig

menu, under the 3rd heading “Communication Protocols”.

The temperature sensor can be examined in the raspberry pi configuration with the command ls/sys/bus/w1/devices. There you should see a device listed such as “28 − 3c01b556d3de⁰⁰. The output is stored in a file called “w1 slave⁰⁰, and will be

accessed automatically by the temperature polling script in the repository.

The temperature sensor connects to the labelled temperature interface on the Piponic

PCB.

### 4.7 Leak Sensor

The leak sensors require minimal setup. They get connected to the ADC, 3.3V and

GND labelled leak header pins on the PCB.

### 4.8 Water Level Sensor

The water level sensor has a breakout board with a reset button on it. This button should be set when the sensor is reading the water level as present (reset-high).

This breakout board connects to the PCB with Data, 5V and GND through the

pre-existing header pins.

### 4.9 pH Sensor

The pH sensor has a breakout board with a BNC edge-connector for the pH probe.

This BNC connector must be passed through the body of the enclosure, so that the

pH sensor can connect to the it on the outside of the enclosure. The breakout board

needs to be connected to the PCB with female to male wires.

### 4.10 Chemical solution preparation and placement

The user must prepare a KOH solution. The concentration of the solution must be

entered into the app. The input part of the pump must be in the KOH solution.

If the setup matches what is shown in the user manual, the user has successfully

passed this validation test.

## 5 Hardware Setup


Figure 3: Enclosure elements inside enclosure: Power Supply, Breadboard, Relay Block, Terminal Block, Raspberry Pi, Water-level board, pH sensor board.

The hardware BOM can be seen in the table below.

Designator | Description | Quantity | Link
Enclosure | 8x8x4’ junc-tion box | 1 | https://www.homedepot.ca/product/1000403713 (https://www.homedepot.ca/product/carlon-thermoplastic-junction-box-8x8x4-in/1000403713)
Heatshrink | Variety Pack | 1 | https://leeselectronic.com/en/product/15370-kit-heatshrink-variety-pack-170pcs. html (https://leeselectronic.com/en/product/15370-kit-heatshrink-variety-pack-170pcs.html)
Cable Gland | 7mm | 3 | https://leeselectronic.com/en/product/html (https://leeselectronic.com/en/product/61270-fitting-water-proof-pg-7-light-grey-csa-bimed-bsr-11.html)
Cable Gland | 9mm | 6 | https://leeselectronic.com/en/product/6125-fitting-water-proof-pg-9-black.html (https://leeselectronic.com/en/product/6125-fitting-water-proof-pg-9-black.html)
Screws/Bolts | 4x1/2”, 6x1/2” | Box

carlon-thermoplastic-junction-box-8x8x4-in/

61270-fitting-water-proof-pg-7-light-grey-csa-bimed-bsr-11.

Table 5: Hardware BOM required for building project


Figure 4: Labelled Enclosure elements: Power Supply, Breadboard, Relay Block, Terminal Block, Raspberry Pi, Water-level board, pH sensor board.

The components within the enclosure must be mounted onto a board that rests

within the enclosure. This board can be fastened to the bottom of the enclosure

with magnets, velcro, or another temporary adhesive of your choosing.

This board can be made of any non-conductive material, such as plastic or wood.

## 6 Software Setup

There are three public GitHub respositories that host our software. Each of reposito-

ries provide setup and installation procedures in their respective READMEs. These

procedures can be followed to setup this project’s software. The three repositories

are as follows:

- piponic (https://github.com/jaydenleong/piponic). This repository con-

tains the Raspberry Pi code associated with the sensing and control system.

- piponic cloud (https://github.com/jaydenleong/piponic_cloud). This

repository contains the server-side code associated with the cloud-based func-

tionality of this project

- piponic app (https://github.com/jaydenleong/piponic_app). This repos-

itory contains the mobile application code.

Lastly, note that some helpful instructions to set up a Raspberry Pi are also included

in Appendix A: RaspberryPi Setup.

## Appendix A: RaspberryPi Setup

The user must be able to properly load the SD card with the RaspberryPi OS using

the Raspberry Pi Imager. Download and install Raspberry Pi Imager, (https://www.raspberrypi.org/software/) select the

Raspbian OS and write it into the SD card.This process will take several minutes.

Using an SD card adapter, the user will be able to see the files that were written into the SD card. They must add/edit 4 files. Firstly, the user must add an

empty text file named ”ssh.txt”. Secondly, the user must add a .conf file named

”wpa supplicant.conf”. This file contains the following text below with the appro-

priate changes to ssid and psk:

country=CA

ctrl_interface=DIR=/var/run/wpa_supplicant GROUP=netdev

update_config=1

network={

scan_ssid=1

ssid="your_wifi_ssid"

psk="your_wifi_password"
}

If the user is not located in Canada, they must replace ”CA” with their appropriate

country code.

Thirdly, the user must edit ”config.txt” by adding the line dtoverlay=dwc2 to the

very bottom of the file. Lastly, the user must edit ”cmdline.txt” and insert modules-

load=dwc2,g ether right after the word rootwait.

After downloading and installing PuTTY (https://www.putty.org) and powering up the RaspberryPi, open

PuTTY and type ”raspberrypi” in the Host Name and click open. A terminal will

open asking for the login credentials. If this does not open a terminal, verify that

the RaspberryPi is connected to the wifi by checking the router. Under device

connected, the user should be able to see the RaspberryPi if the earlier steps were

done correctly. If the RaspberryPi is connected to the wifi, but the terminal still does not open, type the IP address of the RaspberryPi in the host name instead.

This can be found by checking the router as well. Once the terminal is open, enter

the login credential user as ”pi” and the password is ”raspberry”. To verify the

connectivity of the RaspberryPi to the internet, type ”ping 8.8.8.8” in the terminal

and press enter. If a signal is seen, the user has successfully passed this validation

test.

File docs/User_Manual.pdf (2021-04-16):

# IoT Monitoring of Aquaponic and

# Hydroponic Food Production

# USER MANUAL

### UBC Electrical and Computer Engineering Capstone 121

Carson Berry

Lynes Chan

Mason Duan

Jayden Leong

Hannah Xu

for

UBC SEEDS Sustainability Program

Bernhard Nimmervoll, UBC Mechanical Engineering

### April 13, 2021

## Contents

1 Change Log | 3
2 Introduction | 4
3 Installation | 4
4 Operation | 4
5 Maintenance | 12

## 1 Change Log

The change log documents changes made to the document.

Table 1: Change Log of Document
Date | Author | Sections | Change
2021-01-23 | CB | 1.0 - 4.0 | Creation of document skeleton
2021-04-11 | LC | 5.1 | added pH calibration
2021-04-11 | CB | 5.2 | Part Replacement Policies
2021-04-13 | MD | 4.0 | Mobile Application Operation

## 2 Introduction

This User Manual is designed to walk a person unfamiliar with wireless technology

through the steps of setting up, using, and maintaining a monitoring and control

system for their pre-existing aquaponic or hydroponic growing system.

## 3 Installation

For installation instructions, please refer to the Installation Guide Document.

## 4 Operation

To control the actuators and view the sensor values of the PiPonic system, the

user would have to use the companion mobile application. The PiPonic appli-

cation is a mobile application that, in conjunction with a raspberry pi, sensors, and actuators, monitors an aquaponic/hydroponic system. In the PiPonic applica-

tion, the user is able to create an account and is able to view and manipulate the aquaponic/hydroponic systems associated with that account. The application also

allows users to add existing aquaponic/hydroponic systems to their account granted

they know the existing aquaponic/hydroponic’s unique identification.

### 4.1 Launching Mobile Application

In the application drawer of the mobile device, the PiPonic application should be

within the already downloaded applications. The application icon should be the

same as the image below in Figure 1.

### 4.2 Splash Screen

After selecting the PiPonic application, the application’s splash screen will appear as

seen in the image below in figure 2. The user’s credential, if the user has previously

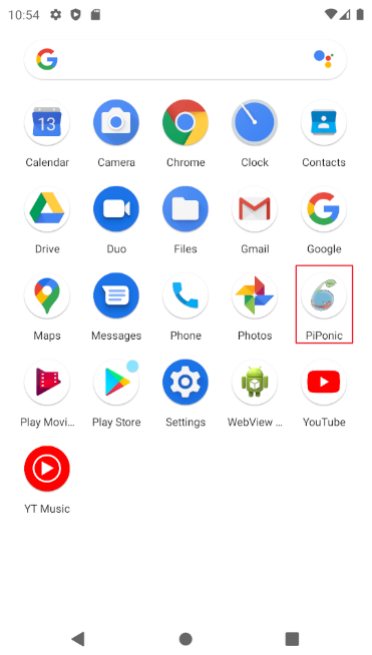
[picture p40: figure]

Figure 1: PiPonic application in application drawer

logged into the application, will be loading in the background of this screen. The

splash screen should be visible for approximately a couple of seconds. After the

splash screen finishes loading, the application would then take the to different screens

depending on if the user has previously logged in the application or not. If the user

has not previously logged in the application, then the user will be brought to the

sign in and sign up screen. If the user has previously logged in the application, the

application will bring the user to the home screen.

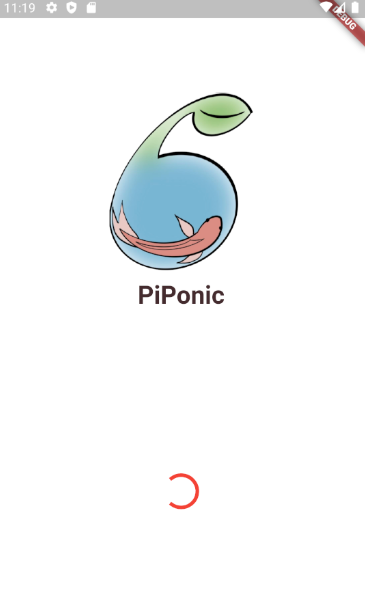
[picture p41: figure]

Figure 2: PiPonic splash screen

### 4.3 Sign In and Sign Up Screen

The sign in and sign up options screen will be presented to users who aren’t pre-

viously authenticated on the application. The sign in and sign up options screen

will give the user the option to either sign up for an account or login to an existing

account. The user can sign up with the application by providing an email and pass-

word or by signing in using an existing account. An image of the application’s sign

in and sign up options screen can be seen below in figure 3.

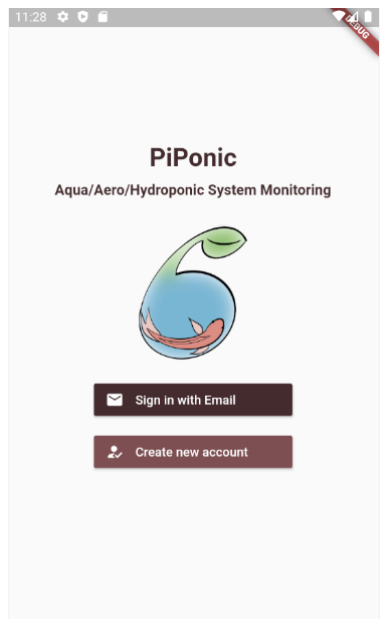
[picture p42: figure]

Figure 3: PiPonic sign-in and sign-up screen

### 4.4 Sign In Screen

The sign in screen is presented when the user taps on the ”Sign in with Email”

option in the sign in and sign up options screen. This page contains two input fields

for the email address and password. Unsuccessful authentication submissions won’t

let the user into the application whereas successful authentication submission will

direct users to the application’s home screen. The email input box verifies that it’s

a valid email address by checking if the ’@’ character is present within the email

submission. Similarly password input box verifies that the password is sufficient by

the password length is at least 6 characters. An image of the sign in screen can be

seen below in figure 4.


Figure 4: PiPonic sign in screen

### 4.5 Sign Up Screen

The sign up screen is presented when the user taps on the ”Create new account”

option in the sign in and sign up options screen. This page contains two input

fields for the email address and password. Unsuccessful sign up submissions won’t

let the user into the application whereas successful sign up submission will direct

users to the application’s home screen. The email input box veries that it’s a valid

email address by checking if the ’@’ character is present within the email submission.

Similarly password input box veries that the password is sucient by the password

length is at least 6 characters. An image of the sign up screen can be seen below in

figure 5.


Figure 5: PiPonic sign up screen

### 4.6 Home Screen

The home screen is presented when the user successfully authenticates with the

application. The home screen will differ in appearance depending on whether or not the user has any existing aquaponic/hydroponic system(s) associated with their

account.

### 4.6.1 No Existing Aquaponic/Hydroponic System(s)

If there are no existing aquaponic/hydroponic system(s) associated with the users ac-

count, the home screen (and every subsequent tab in the bottom navigation bar) will

just show a page where the user is able to enter an aquaponic/hydroponic ID. Here

the user is able to enter the unique identification of an existing aquaponic/hydroponic

to their account. An image of the screen where the user can add an existing aquaponic/hydroponic system to their account can be seen below in figure 6.

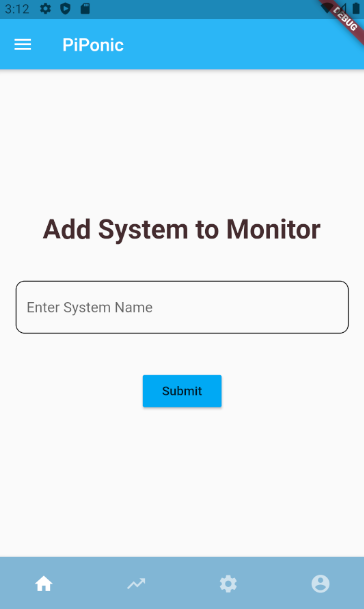
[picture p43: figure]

Figure 6: No existing aquaponic/hydroponic system(s)

### 4.6.2 Existing Aquaponic/Hydroponic System(s)

If there are existing aquaponic/hydroponic system(s) associated with the users ac-

count, the home screen will show a summary of one of the existing systems. The

home page would show a summary of the chosen system including the name of the

system, the status of the system, last time the information was updated, the warn-

ings for the system, and a list of all the sensors and it’s measured values. An image of the home screen with the summary of an aquaponic/hydroponic system can be

seen below in figure 7.


Figure 7: Home screen with existing aquaponic/hydroponic system(s)

### 4.7 Aquaponic/Hydroponic List

Taping on the hamburger menu button on the top left of the application, the list of the user’s aquaponic/hydroponic systems will slide out. Here the user is able to

switch between the different aquaponic/hydroponic systems associated with their

account. An image with the location of the hamburger menu button and the list of the user’s aquaponic/hydroponic systems is shown below in figure 8.

### 4.8 Chart Screen

Tapping on the rising trend icon in the bottom navigation bar brings the user to the

chart screen where the user is able to see a chart of their sensor values and the time

at which they were measured. Here the user is able to change the different sensors


Figure 8: Location of the hamburger menu button and the list of the user’s aquaponic/hydroponic systems

that they want to see and are also able to change the range of time for which the

measurements were taken. A screenshot of the charts screen can be seen below in

figure 9.

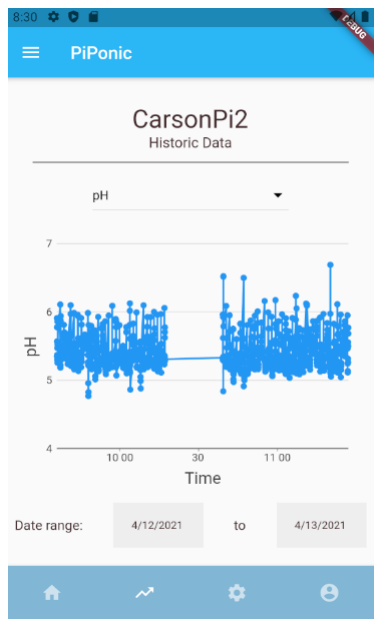
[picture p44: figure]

Figure 9: PiPonic Chart Screen

### 4.9 System Settings Screen

Tapping on the gear icon in the bottom navigation bar brings the user to the aquaponic/hydroponic system setting page. Here the user can set the range of

acceptable values for the aquaponic/hydroponic sensors and well as calibrate the

pH sensor. The user can also change the sensor measurement interval by clicking on the ”General” tab on the screen. A screenshot of the aquaponic/hydroponic settings

screen can be seen below in figure 10.


Figure 10: PiPonic system settings screen

### 4.10 User Settings Screen

Tapping on the user icon in the bottom navigation bar brings the user to the user settings page. Here the user can add additional aquaponic/hydroponic systems to

their account to monitor and control. The user can also logout of their account and

delete their account. A screenshot of the user settings screen can be seen below in

figure 11.


Figure 11: PiPonic user settings screen

## 5 Maintenance

### 5.1 pH Calibration

The pH sensors must be calibrated every month. Before calibration, the user must

have 2 solution with distinctively different pH values. The most common solutions

that can be bought are solutions with pH of 4,6, or 7. Navigate through the app to

reach the pH calibration screen.

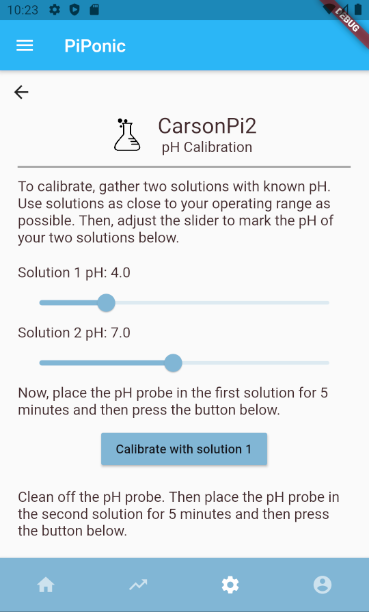
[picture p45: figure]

Figure 12: pH Calibration Screen

There are 2 pH sliders for the 2 solutions the user has. Make sure that the pH values

match the pH for the solutions being used. Place the pH probe in solution 1 and

mix it around for a few seconds. Then press the ”Calibrate with solution 1” button

on the app. Wait for 5 minutes, then take the pH probe, clean it, then place the pH probe in solution 2. Press the ”Calibrate with solution 2” button the app and wait

for 5 minutes.

Once this process is finished, the user has successfully calibrated the pH sensor.

### 5.2 pH Solution

We recommend alternating between potassium hydroxide (KOH) and calcium hy-

droxide (CaOH) as a basic solution to add to your system. This can be done in 1

gallon increments, which should last about a week.

### 5.3 Part Replacement

Some items have limited lifespans, such as the back-up batteries and the pH-sensor.

The back-up batteries should be replaced after their combined voltage drops below

1V.

The pH sensor should be replaced after 1 year of use, or if the user notices that it

is no longer maintaining stable measurements, or accurately measuring pH.

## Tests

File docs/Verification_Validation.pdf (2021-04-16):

# IoT Monitoring of Aquaponic and

# Hydroponic Food Production

# Verification and Validation

### UBC Electrical and Computer Engineering Capstone 121

Carson Berry

Lynes Chan

Mason Duan

Jayden Leong

Hannah Xu

for

UBC SEEDS Sustainability Program

Bernhard Nimmervoll, UBC Mechanical Engineering

### April 13, 2021

## Contents

1 Overview | 3
2 Verification | 4
3 Validation | 22

## Revision History

Date | Author | Sections | Change
2020-10-05 | JL | 1.0 - 4.0 | Creation of document skeleton
2020-10-16 | MD | 1.0 - 4.0 | First draft
2020-11-28 | CB | 2.0 - 4.0 | Added subsystem specifics test outlines
2021-01-15 | CB | 3.0 | Restructuring document to reflect design and re-quirements
2021-02-19 | CL | 1.0 - 6.0 | Added section 6.0 Validation and minor changes to earlier sections to be consistent with the require-ments documentation
2021-02-19 | JL | 2.0 - 3.0 | Reworded overview section to be more concise. Updated testing section to be more concise, and match updated functional requirements. Removed some outdated tests due to changed requirements.
2021-04-11 | JL | 1.0 - 3.0 | Major revisions to all sections for Milestone 4.

## 1 Overview

This document outlines the verification and validation plans for our project, an IoT hydroponic or aquaponic monitoring system. The verification tests and results included in this document seek to prove that our project meets its requirements. For more information about these requirements, please see the included Requirements document.

The design of our project informs the structure of the verification testing and results below. Our hydroponic and aquaponic monitoring system contains three main subsystems seen in Figure 1: a sensing and control system, cloud infrastructure, and a mobile software application. As such, our verification tests and results will be organized under each of these subsystems.


Figure 1: System Level Block Diagram

Additionally, this document outlines our project’s validation plan, to ensure the project meets our client and user’s needs. To see our validation tests and results, please see section 3.

Finally, please note that this document assumes that the reader is familiar with the setup of our design described in System Installation document. As well, we assume that the reader is familiar with the design described in the Design document. If this is not the case, we strongly recommend reading those documents before reading the tests described here.

## 2 Verification

This section provides verification tests and results for the following main subsystems in our design:

- Sensing and Control System
- Cloud Infrastructure
- Software Application

### 2.1 Sensing and Control System Verification

The sensing and control system has two functions. First, it measures important system variables including water pH, level, temperature, and leakage. It then sends these measurements to the Cloud Infrastructure so users can monitor their aquaponic or hydroponic system. Second, the sensing and control system automatically controls pH and water level to ensure user’s aquaponics or hydroponics systems remain healthy. Please consult Figure 2 below and the Design document for more details about the sensing and control system.

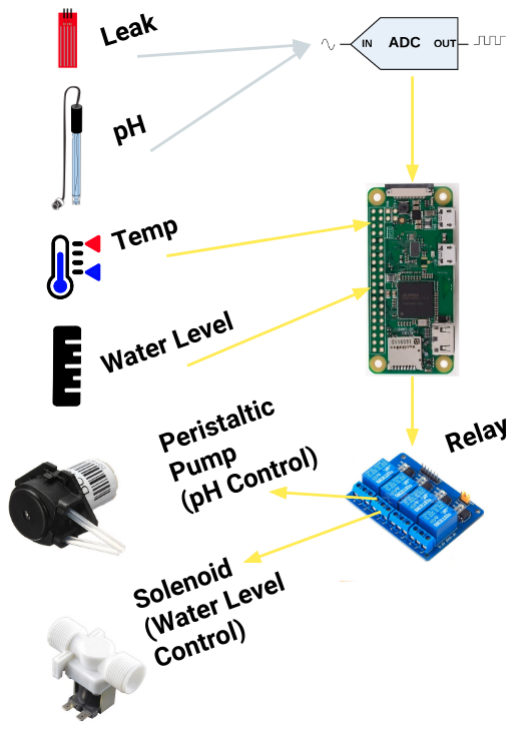
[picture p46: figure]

Figure 2: Overview of the sensing and control subsystem.

For an overview of all the verification tests performed on the sensing and control subsystem, please consult Table 1 below. Each of these tests in described in further detail in the proceeding subsections.

Table 1: Sensing and Control Verification Test Overview.

Test | Purpose | Requirement(s) | Result
SCT1 | Sensors measurements can be made and send to the Cloud Infrastructure | F2 | PASSED
SCT2 | pH and water level are maintained in healthy ranges automatically | F4 | PASSED
SCT3 | Operates on backup power | F5 | PASSED
SCT4 | The sensing and control system is water resistant | NF4 | PASSED

SCT1: Sensors measurements can be made and send to the Cloud Infrastructure

Purpose

Be able to send sensor measurements to users. Also, to test whether sensors can be read.

Procedure

1. Run the sensing and control system
2. Follow the testing procedure in CT1 to ensure messages are recieved by the cloud correctly. Otherwise, the test FAILED.

Result

The test PASSED.

SCT2: pH and water level are maintained in healthy ranges automatically

Purpose

To make sure that pH and water level are controlled to be within healthy levels.

Procedure

1. Place the pH probe in an acidic solution.

2. Place the one end of the peristaltic pump in a basic solution and the other in the same solution as the pH probe.
3. Run the sensing and control system, and ensure that the pH stabilizes at the target pH set in the mobile application.
4. Place the water level sensor outside of water.
5. Ensure that the solenoid turns on periodically to simulate adding more water to the hydro/aquaponics system.

Result

The test PASSED.

SCT3: Operates on backup power

Purpose

To ensure that our system can remain operational in the case of a power failure.

Procedure

1. Connect 2AA batteries into the 5V boost converter board.
2. Verify that the boost converter is able to output 5V DC with a multimeter. If not, test FAILED.
3. Simulate the 5V boost converter shutdown circuit’s functionality, as seen in Figure 3.

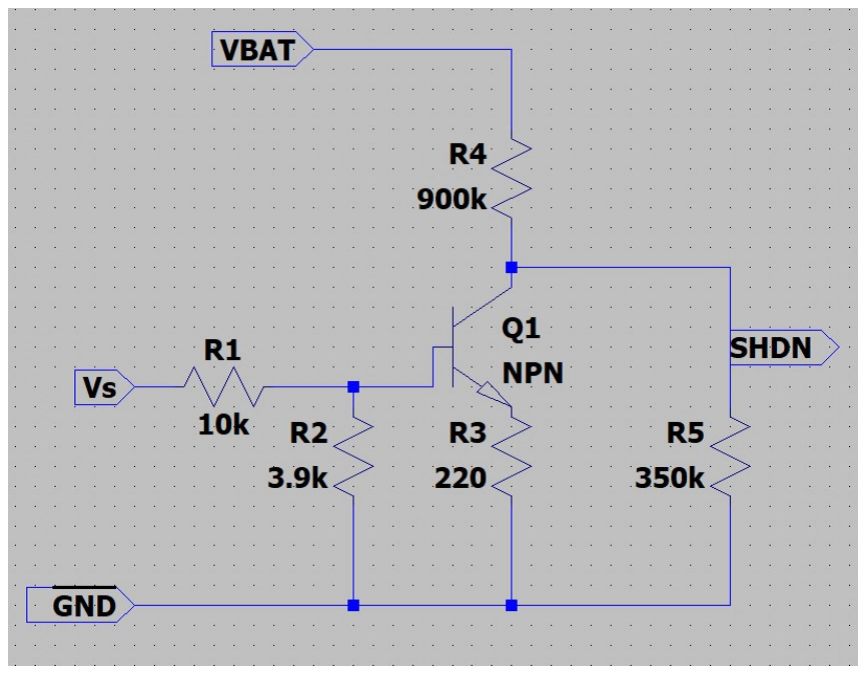
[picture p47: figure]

Figure 3: Boost converter shutdown circuit. This circuit disables the AA batteries when 12V is present.

4. Ensure that the circuit simulation outputs a low voltage when the 12V power supply is present and a ‘high’ voltage (above 0.8V) when the 12V power supply is absent. A plot of this behaviour can be seen in figure 4. If this behavior is not seen, the test FAILED.

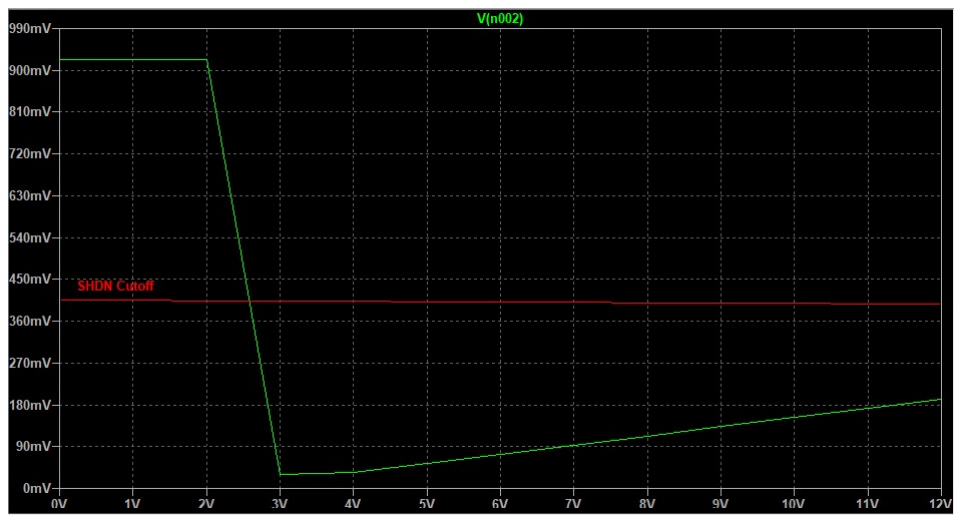
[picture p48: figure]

Figure 4: 5V boost converter shutdown circuit output vs source voltage. We see that once the source voltage (normally 12V) drops below 3 V, the SHDN signal goes high.

5. Construct the physical circuit.
6. Attach a multimeter voltage probe to the 5V rail and GND.
7. Plug in the 12 V power source
8. Connect 2AA batteries to the 5V boost converter.
9. Ensure that when 12V is present, the voltage rail read 4.7V. Otherwise, the test FAILED.
10. Ensure that when the 12V power supply is disconnected, or unplugged, the voltage rail should now read 5V. Otherwise, the test FAILED.

Result

The test PASSED.

SCT4: The sensing and control system is water resistant

Purpose

The purpose of this is to ensure that the sensing and control system is water resistant. This is important for aqua/hydroponics systems that are around water, or are perhaps placed outside.

Our system must comply with a rating of IP64. This means that the enclosure must be protected from low pressure water jets in any direction.

Procedure

1. Spray the enclosure with a shower head for 15 minutes from all directions
2. Ensure not liquid was able to enter the enclosure. If not, the test FAILED

Result

The test PASSED.

### 2.2 Cloud Infrastructure Verification

The cloud infrastructure connects the software application with the sensing and control system. This means that it provides the following functionality:

- Passing data beztween the software application and the sensing and control system.
- Sending notifications to the software application if there are issues detected by the sensing and control system.
- Saving sensor measurements in a database.

For an overview of the Cloud Infrastructure, please see Figure 5 below:

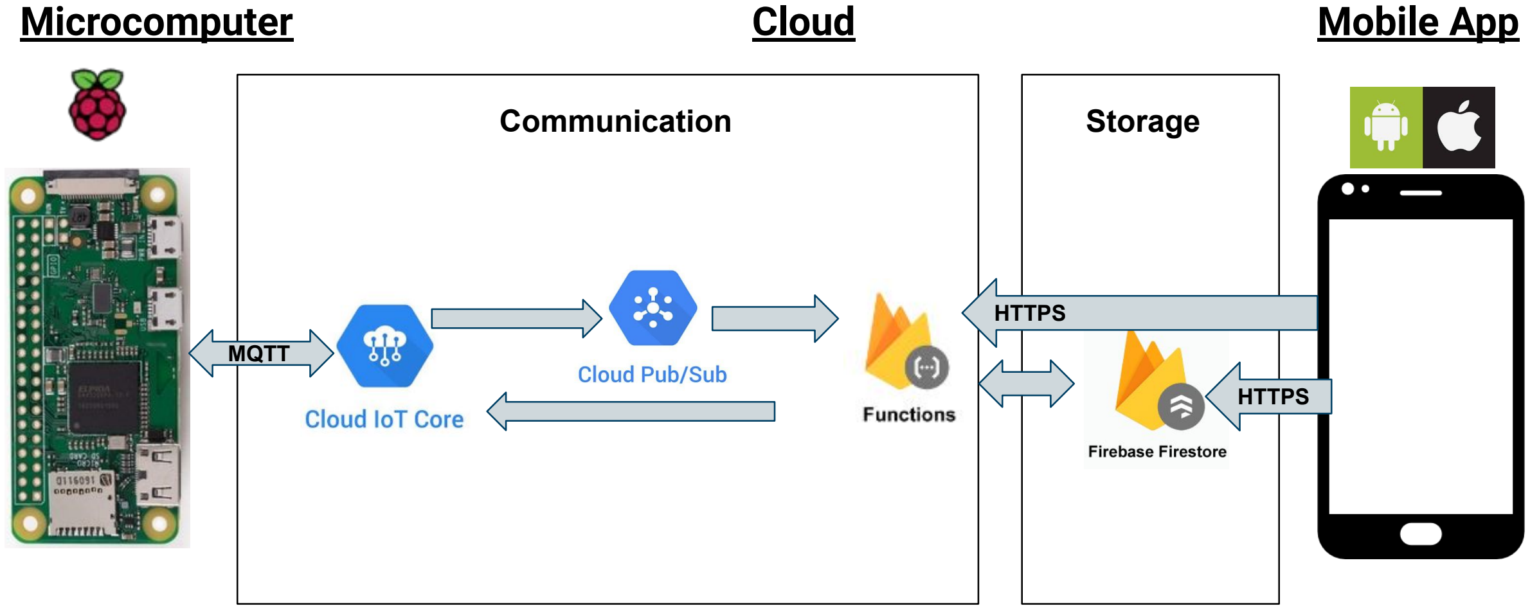
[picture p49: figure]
Microcomputer; Cloud; Mobile App; HTTPS; MQTT; Communication; Storage

Figure 5: Overview of the cloud infrastructure.

For an overview of the tests performed on the cloud infrastructure system, please see Table 2 below.

Table 2: Cloud Infrastructure Verification Test Overview.

Test | Purpose | Requirement(s) | Result
CT1 | Messages from sensing and control system are saved in a database | F1, F2 | PASSED
CT2 | Detects when sensor readings are outside the normal range | F3 | PASSED
CT3 | Send configuration messages to the sens-ing and control system | F3 | PASSED

CT1: Messages from sensing and control system are saved in a database

Purpose

Ensures that sensor measurements from an aqua/hydroponic system are saved properly. This allows the mobile application to display the status and history of an aqua/hydroponic system.

Procedure

1. Set the sensor update interval to be 1 minute using the mobile application.
2. Run the sensing and control system so sensor measurements being made
3. Go to the Firebase web console for the project.
4. Select the Firestore Database tab.
5. Select the Status collection to display the most recent sensor readings stored in the database.
6. Verify that sensor measurement are updating every 1 minute. If not, test FAILED.
7. Select the History collection to display past measurements of an aqua/hydroponic system.
8. Verify that new sensor measurements are being written to the database every 1 minute. If not, test FAILED.
9. Verify that all sensor measurements are saved in the database. If not test FAILED.
10. Test PASSED if no failures detected above.

Result

In Firestore, updates can be seen as new data flashes as orange when recieved. This can be used to check whether messages have been updated in the Status and History collections. See Figure 6 for an example of what this looks like.

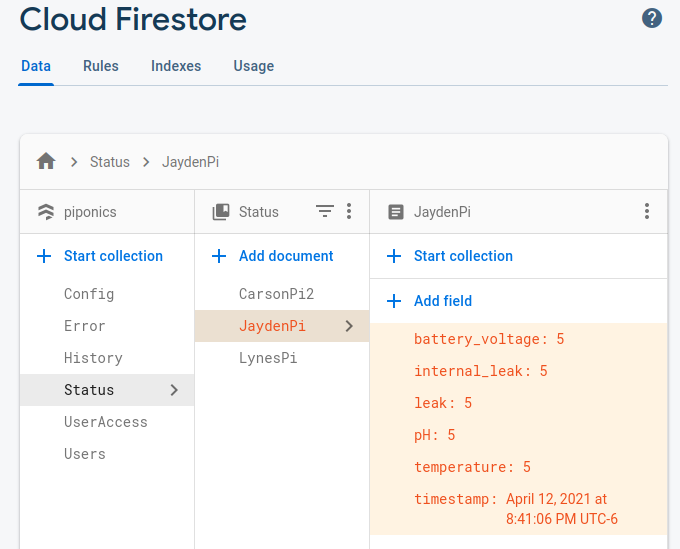
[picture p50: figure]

Figure 6: Firestore database updating during CT1

After running this test, it PASSED.

CT2: Detects when sensor readings are outside the normal range

Purpose

Ensures abnormal sensor readings are detected. For example, the system should detect if there is a leak or if the temperature is too low.

Procedure

1. Go to the Firebase web console for the project.
2. Select the Firestore Database tab.
3. Select the Error collection to display whether an error is detected on a given aqua/hydroponic system.
4. Place the pH probe in an acidic solution.
5. Ensure that the PH LOW field is true. If not, test FAILED.
6. Place the water temperature sensor in ice water. Ensure that the the TEMP LOW field is true. If not, test FAILED.
7. Repeat the same process for all sensors to generate errors. Ensure that the appropriate errors are detected. If not, test FAILED.

8. If no failures detected above, test PASSED.

Result

Please see Figure 7 below for a demonstration of the test. As you can see, the system has detected that the water temperature is low, and there are multiple leaks.

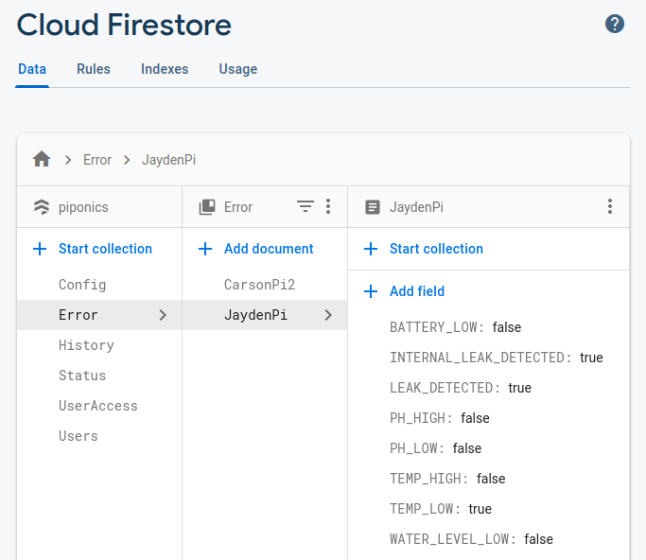
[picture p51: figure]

Figure 7: Firestore database Error collection updating during CT2

All tests PASSED.

CT3: Send configuration messages to the sensing and control system

Purpose

Allows the mobile application to configure settings like the sensor sampling rate and the target pH. This test verifies this functionality.

Procedure

1. Go to the Firebase web console for the project.
2. Select the Firestore Database tab.
3. Select the Config collection to display the configuration settings of an aqua/hydroponic system.

4. Run the sensing and control system and view the logs being outputted in terminal
5. Change the values of each of the configuration values in the Firestore database.
6. Ensure the sensing and control system prints a message with the new configuration values. If values are incorrect or not recieved, test FAILED.

Result

The test PASSED.

### 2.3 Software Application Verification

The software application allows users to monitor their aquaponic or hydroponic system. This includes viewing sensor readings, adjusting system settings, and recieving notification if errors are detected. Please see Figure 8 for demo screenshots of the software application. For more details about the design of the mobile application, please see the included Design document.


Figure 8: Screenshots demonstrating the software application.

For an overview of all the verification tests performed on the software application, please see the Table 3 below.

Table 3: Software Verification Test Overview.

Test | Purpose | Requirement(s) | Result
ST1 | Software application displays most recent sensor readings stored in the cloud | F1 | PASSED
ST2 | Software application displays charts of previous sensor readings | F2 | PASSED
ST3 | Software application can set normal range of aquaponics or hydroponics system vari-ables | F3 | PASSED
ST4 | Software application recieves notifications if sensor readings are outside of a normal range. | F3 | PASSED
ST5 | Software application can be used to cali-brate the pH sensor | F6 | PASSED
ST6 | Software application has an appropriate login system | NF2 | PASSED

In the following subsections, we will describe each software application test in detail.

ST1: Software application displays most recent sensor readings stored in the cloud

Purpose

To ensure aquaponic and hydroponic growers can monitor most recent updates from their system. Therefore, helps verify requirement F1.

Procedure

1. View the most recent data stored in the database. To do this, open the Firebase web console for the project.
2. Select the Firestore Database tab.
3. Select the Status collection to display the most recent sensor readings stored in the database.
4. Check that the values displayed on the mobile application status page match the values in the database. If not, test FAILED.
5. Check that the mobile application status page displays all of the values stored in the database. If not, test FAILED.
6. Check that the “Last Updated” timestamp is correctly updated on the app’s status page. If not, test FAILED.
7. Check that all systems in the database pass the above three tests. If not, test FAILED.
8. If no failures detected above, test PASSED.

Result

See the following screenshot of the database and the mobile application status page for an example of how this test is conducted. This example demonstrates the test using the system called CarsonPi2 :

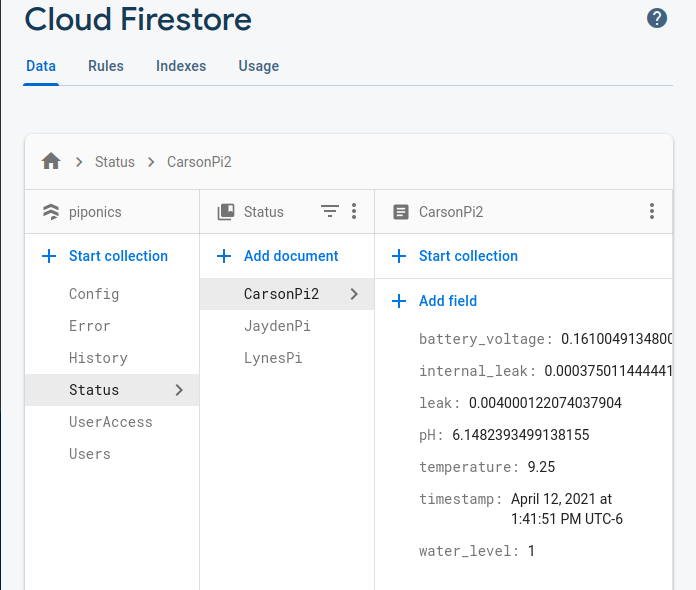
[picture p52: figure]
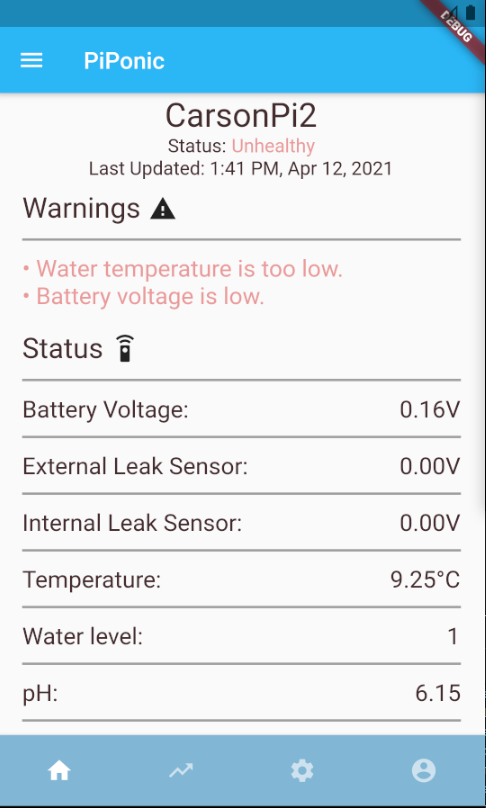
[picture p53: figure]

Figure 9: Screenshots taken during test ST1

These screenshots demonstrate that the test PASSED.

ST2: Software application displays charts of previous sensor readings

Purpose

To allow aquaponic and hydroponic growers to analyze system trends over time. Therefore, helps verify requirement F2.

Procedure

1. Turn the sensing and control system on for 24 hours, allowing the sensor measurements to be recorded.
2. Using the “Status Page” note down the sensor measurements every hour for some 8 hours during that 24 hour period.
3. Open the “Charts Page” on the mobile application by selecting the arrow icon on the bottom panel.
4. For each sensor reading, verify that the sensor values match your recorded values during the 8 hour period. If not, test FAILED.
5. If sensor measurements for each sensor is not displayed for the previous 24 hour period, test FAILED.
6. If no failures detected above, test PASSED.

Result

Below you can see an example of the test running, with the screenshot of the temperature plot in Figure 10. This test also PASSED for all other sensors.

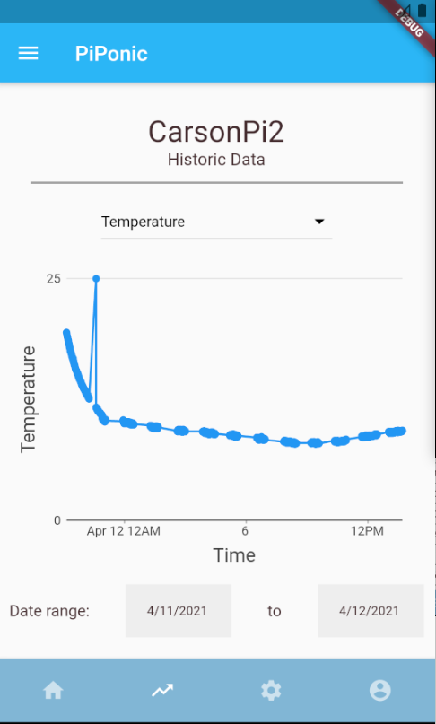
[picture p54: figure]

Figure 10: Software application “Charts Page” displaying temperature during test ST2.

Note that the single spike in temperature was expected as the temperature sensor was temporarily moved to hot water. The final result is that the test PASSED.

ST3: Software application can set normal range of aquaponics or hydroponics system variables

Purpose

This test ensures that users can configure their system’s healthy range. This is used to detect when a system may be unhealthy and report that to a grower.

Procedure

1. Open the Firebase web console for the project.
2. Select the Firestore Database tab to see database values.
3. Select the “Config” collection to see system configuration values

4. Select the gear icon on the bottom tab of the mobile application to open system settings.
5. Click on “General Settings” and adjust the sensor measurement interval slider. Click Submit. Ensure that the update interval minutes field in the database is updated accordingly. Otherwise, test FAILED.
6. Click on pH Settings and adjust the sliders and click submit. Like the point above, ensure the database is updated accordingly. Otherwise, test FAILED.
7. Adjust a slider in the “pH Settings” page, then click cancel. Ensure that slider values return to their previous values. Otherwise, test FAILED.
8. Repeat the two tests above, only for the “Temperature Settings” page.
9. The test PASSED if no failures were detected above.

Result

See the images below for samples of this test, where database values are verified with app configuration settings:

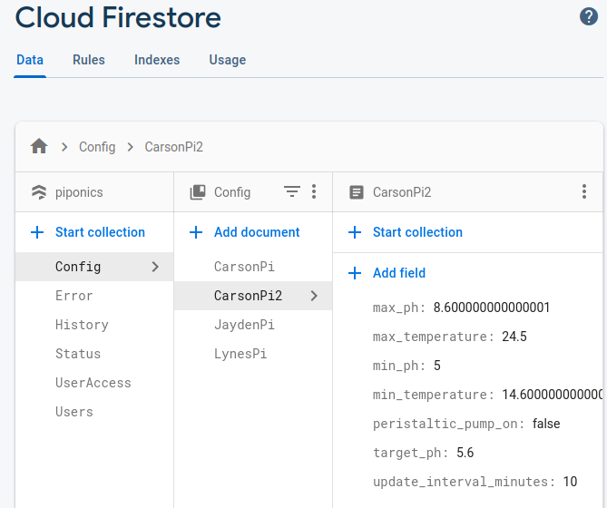
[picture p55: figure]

Figure 11: Screenshots taken during test ST3

When ran, the above test PASSED.

ST4: Software application recieves notifications if sensor readings are outside of a normal range.

Purpose

This test checks whether notifications/alerts are sent to users if sensor measurements from their aqua/hydroponic systems are outside of a normal range. For instance, if the pH is detected to be very acidic (i.e pH = 4), then the user should be alerted with a warning that the pH is too low.

Procedure

1. Spill water on the water leakage sensor. If no push notification recieved by the mobile application, test FAILED.
2. Set the minimum pH to 5. Place the pH probe in pH = 4 solution. If no pH too low notification recieved by the mobile application, test FAILED.
3. Remove backup batteries from the sensing and control system. If no battery low notification recieved by the mobile application, test FAILED.
4. Remove the water level sensor from water. If no water level low notification, test FAILED.
5. Set the minimum water temperature to 10 C. Place the temperature sensor in ice water. If no water temperature low notification, test FAILED.
6. If no failures detected above, test PASSED.

Result

Please see below for a sample image of notifications being received by the mobile application.


Figure 12: App notification screenshot taken during test ST4

This test PASSED when ran.

ST5: Software application can be used to calibrate the pH sensor

Purpose

This test verifies that the pH sensor can be calibrated from the mobile application.

Procedure

1. Open the mobile application and select the settings gear icon on the bottom tab
2. Select the pH calibration setting
3. Follow the instructions on the mobile application page.
4. Place the pH probe in a solution with known pH and ensure the value read on the mobile application matches.

Result

Below in Figure 13, you can see the pH calibration page. We used two solutions to calibrate the pH sensor, with pH = 4 and pH = 7.


Figure 13: pH calibration page during test ST5

Afterward, we placed the pH probe in a solution with pH = 7, and found that the pH reading was accurate. Therefore, this test PASSED.

ST6: Software application has an appropriate login system

Purpose

To verify that users can create their own accounts and login in properly.

Procedure

1. Open the mobile application.
2. Try to login using a random email and password. This should not allow you to login. Otherwise, test FAILED.
3. Create a new account using an email and password.
4. Try to login to the system, but misspell your username. If the app crashes, or allows access to your account, test FAILED.
5. Login to the system using your email and password. If you are not able to login to your account using email and password, then test FAILED.
6. Test PASSED if no failures detected above.

Result

Below in Figure 14, you can see the login pages that were tested using the above procedure.


Figure 14: Login pages during test ST6

All the tests for ST6 PASSED.

## 3 Validation

This section states validation tests and their corresponding results for our project. The purpose of this section is to ensure that our design meets the needs of our users, who are aquaponics and hydroponic growers.

Our validation tests consist of questions asked to users, who provide feedback about the design. Our design has been used by our client over the past two months at his home hydroponics system. The feedback provided in this section will be from his comments. In future, similar questions can be asked to new users too.

Table 4 below provides an overview of our validation tests and their corresponding results.

Table 4: Validation Test Overview.

Test | Req(s) | Purpose | Key User Feedback
V1 | F1 | Viewing system variables | • Add configurable time periods between sen-sor measurements for each sensor.
V1 | F2 | Analyzing system vari-able trends | • Time-averaging data points in sensor mea-surement charts. This helps the user visual-ize trends more clearly.
V3 | F3 | Recieving system alerts | • Verify that notifications are recieved by phones even when the app is not running. • pH and water temperature notifications can be changed to daily notifications instead of immediate notifications.
V4 | F4 | Recalibrating sensors | PENDING
V5 | NF3 | Installation and setup procedures | • Create a short video explaining how to install the system
V6 | All | General feedback | • Adjust the pH only if multiple measurements detect that the pH is low

Please note that this section assumes the reader is familar with the design of our project as outlined in the attached Design document.

### V1: Viewing system variables

Purpose

System variables like water pH, level, temperature and more must be displayed to growers in a clear manner.

Results

In Table 5, we provided validation questions to help us understand whether our design meets our user’s needs. Note that for each question, we asked our client to mention any difficulties he had with our system, or if he had any suggestions for improvements.

Table 5: Questions to validate user experience of viewing system variables.

| Question | User Feedback
Q1 | Were you able to create an account and login? | Yes
Q2 | Were you able to locate all sensor measurements with the app? | Yes
Q3 | Were the sensor measurements easy to interpret and understand? | Yes
Q4 | Were warning messages displayed by the app easy to interpret and under-stand? | Yes
Q5 | Do you have any recommendations about how we might improve how sen-sor readings are displayed? | Read interval should be controllable by sensor. Eg: - spill sensor needs up-dates frequently. Water level sensor may not show low reading for a long time - it only will go low for a short part of the fill/drain cycle.

Analysis

The key recommendation from our client is to add configurable time periods between sensor measurements for each sensor. This allows some sensors (like the water leakage sensor) to be read faster than slower changing variables (like water pH). This improvement can be made in the next iteration of the design.
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

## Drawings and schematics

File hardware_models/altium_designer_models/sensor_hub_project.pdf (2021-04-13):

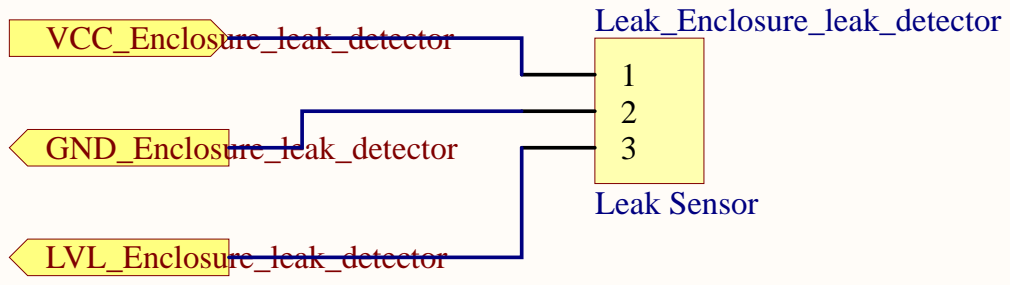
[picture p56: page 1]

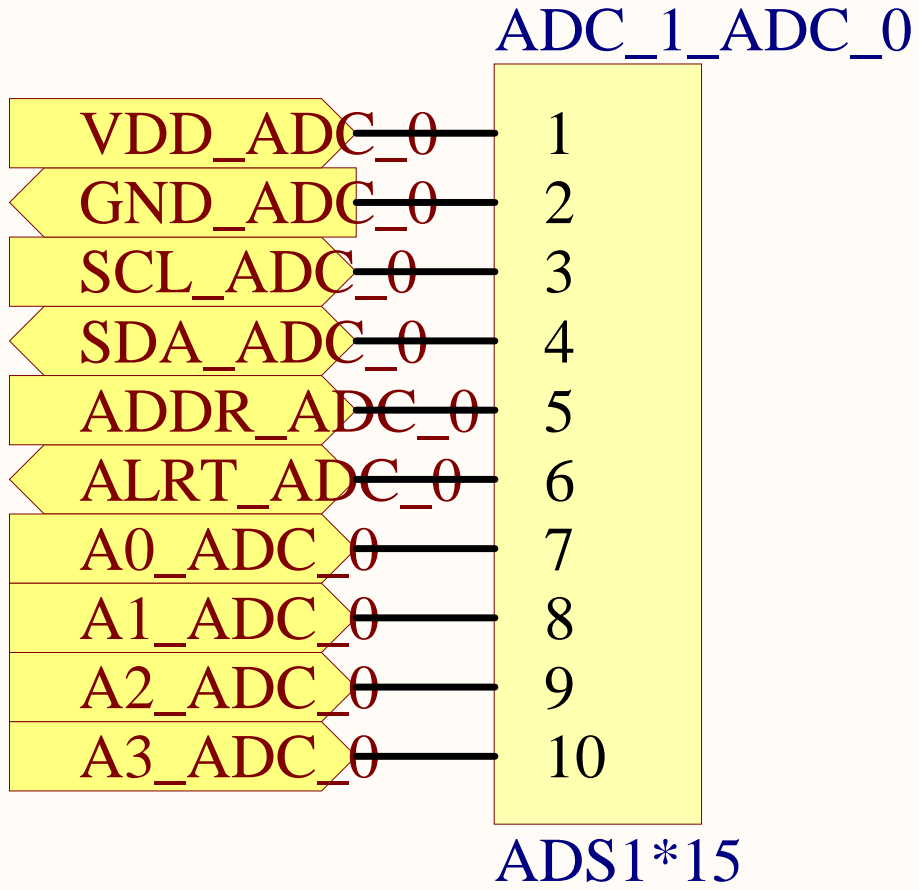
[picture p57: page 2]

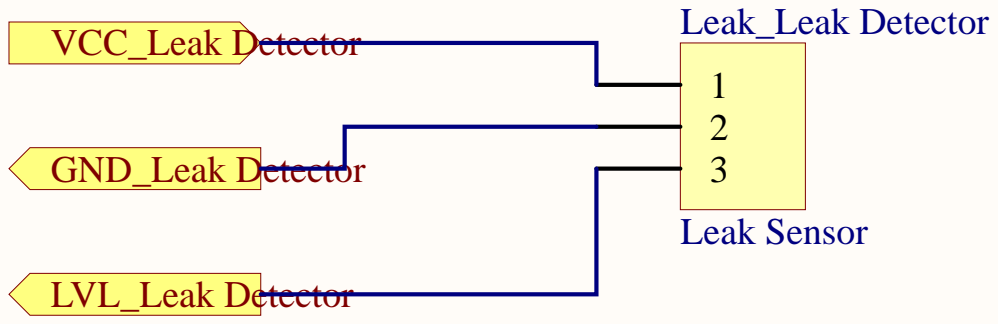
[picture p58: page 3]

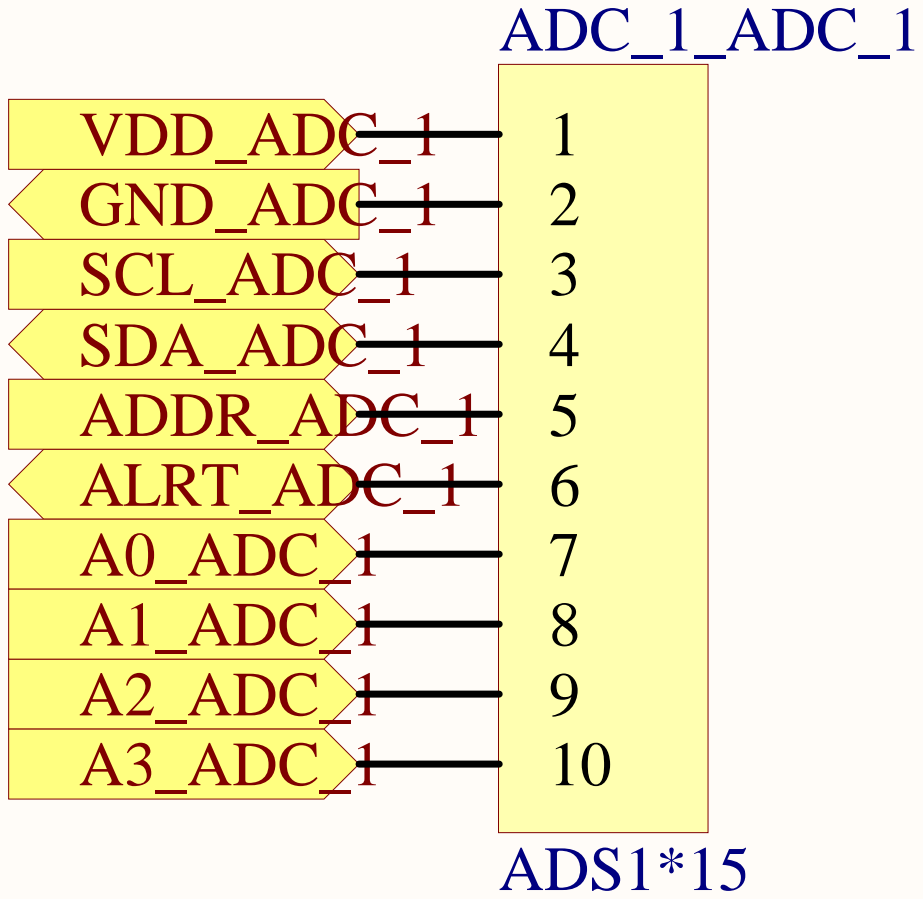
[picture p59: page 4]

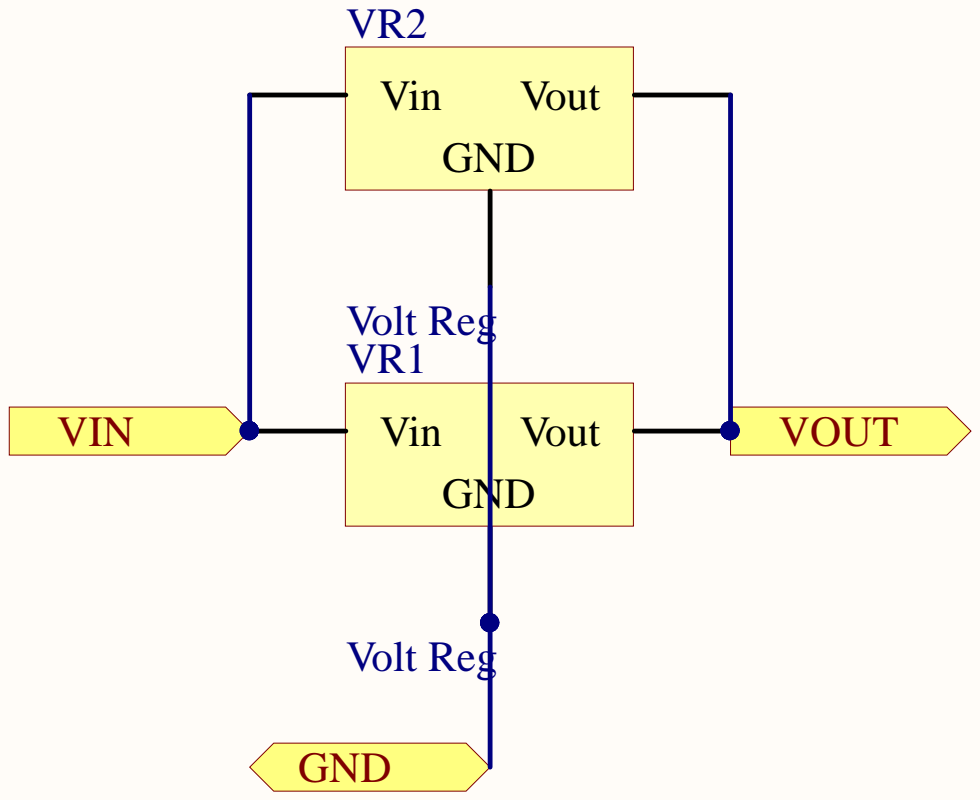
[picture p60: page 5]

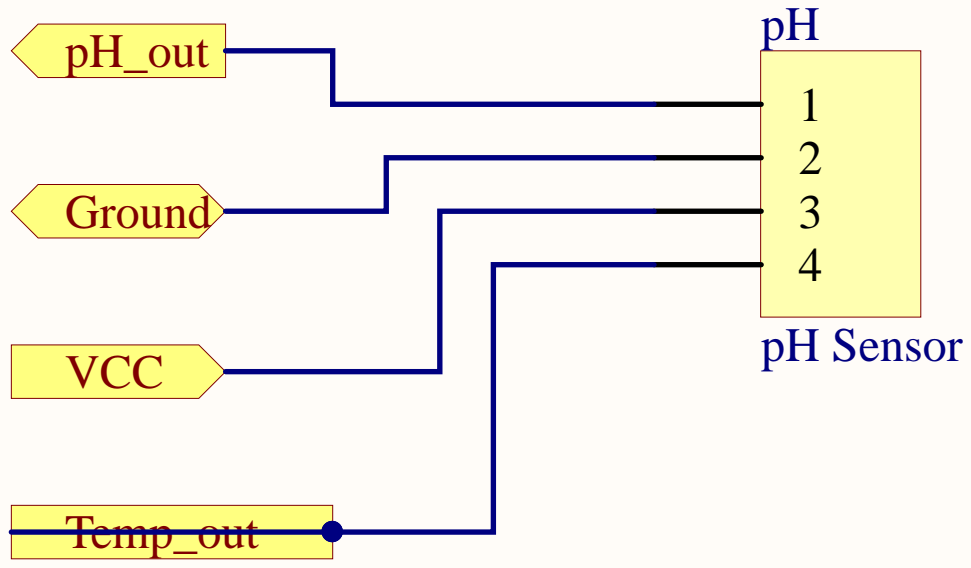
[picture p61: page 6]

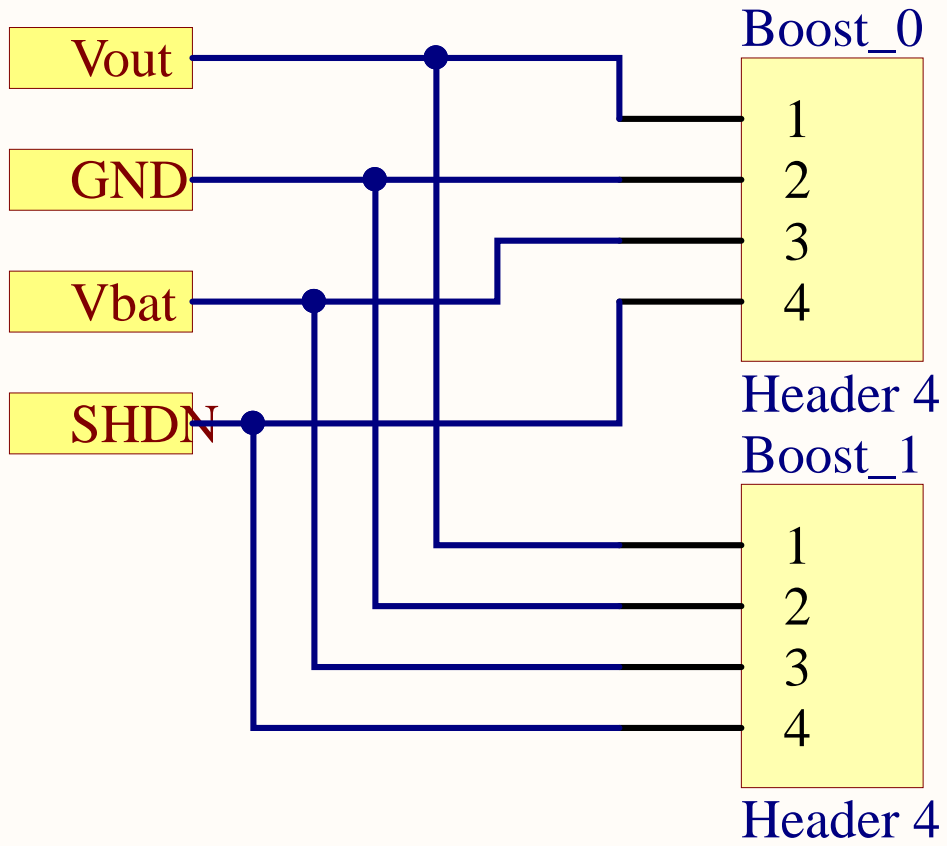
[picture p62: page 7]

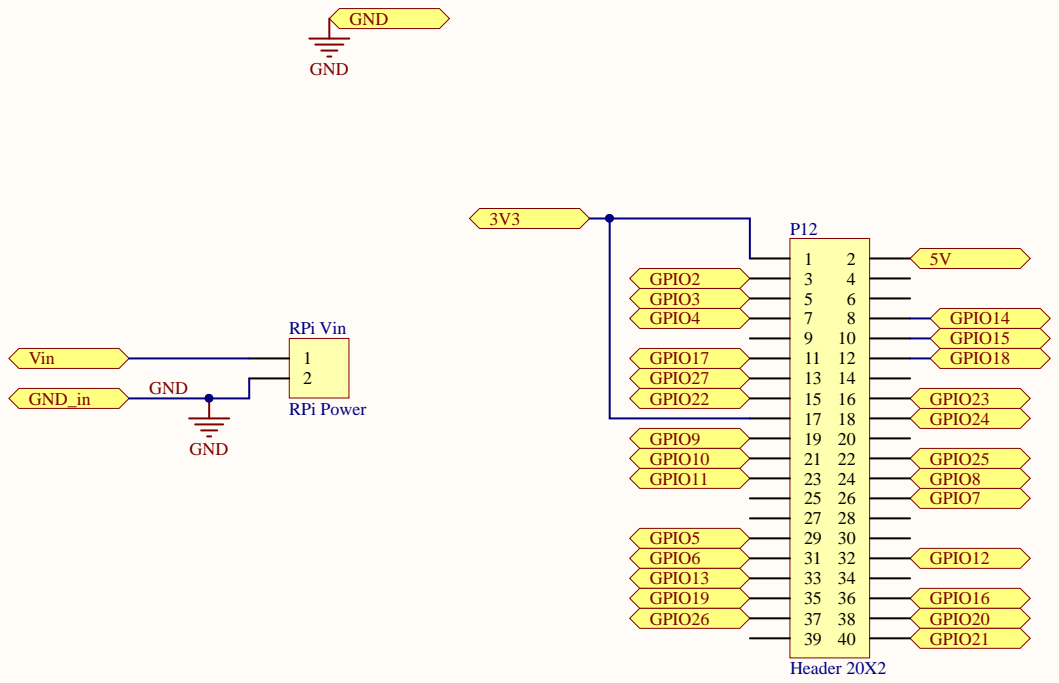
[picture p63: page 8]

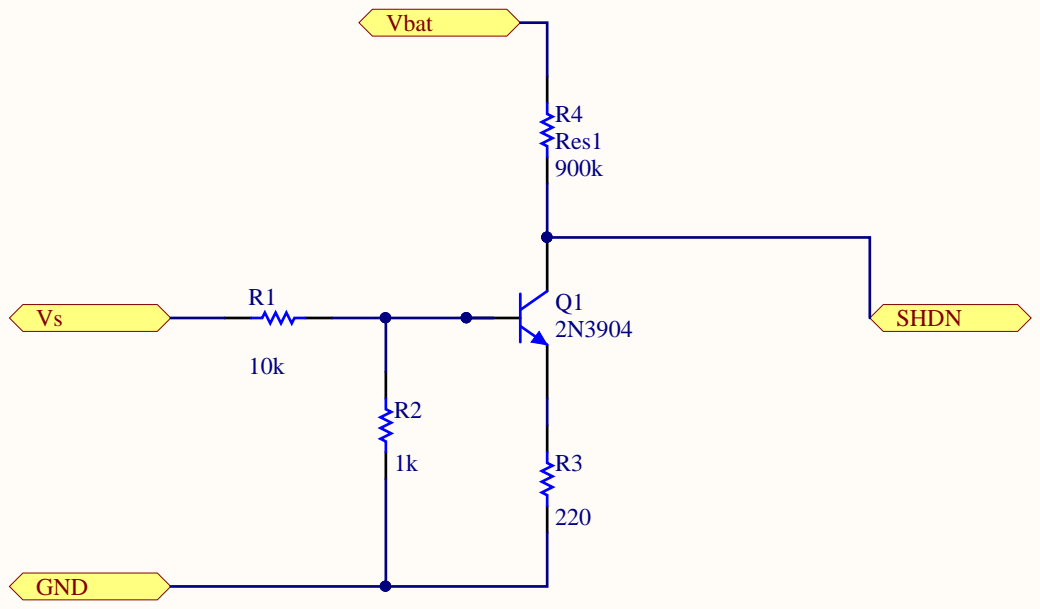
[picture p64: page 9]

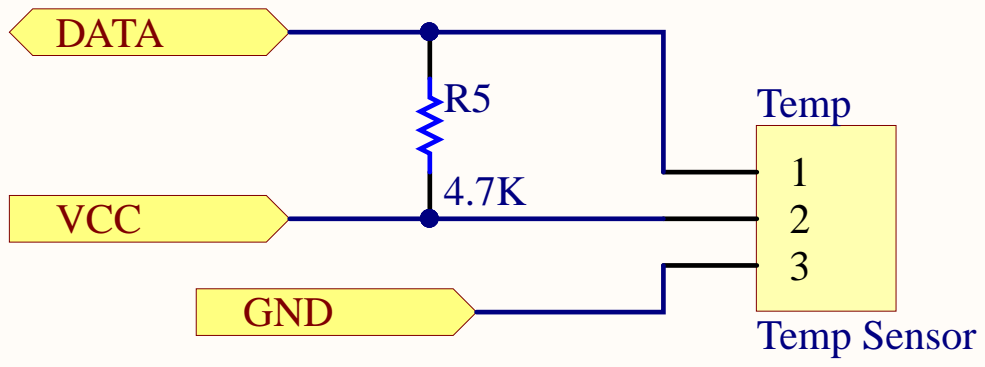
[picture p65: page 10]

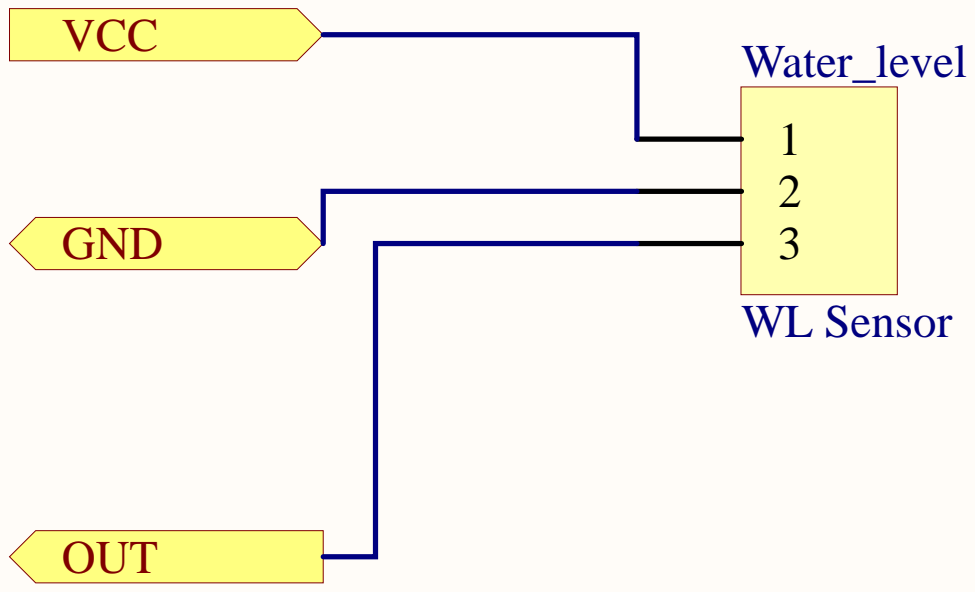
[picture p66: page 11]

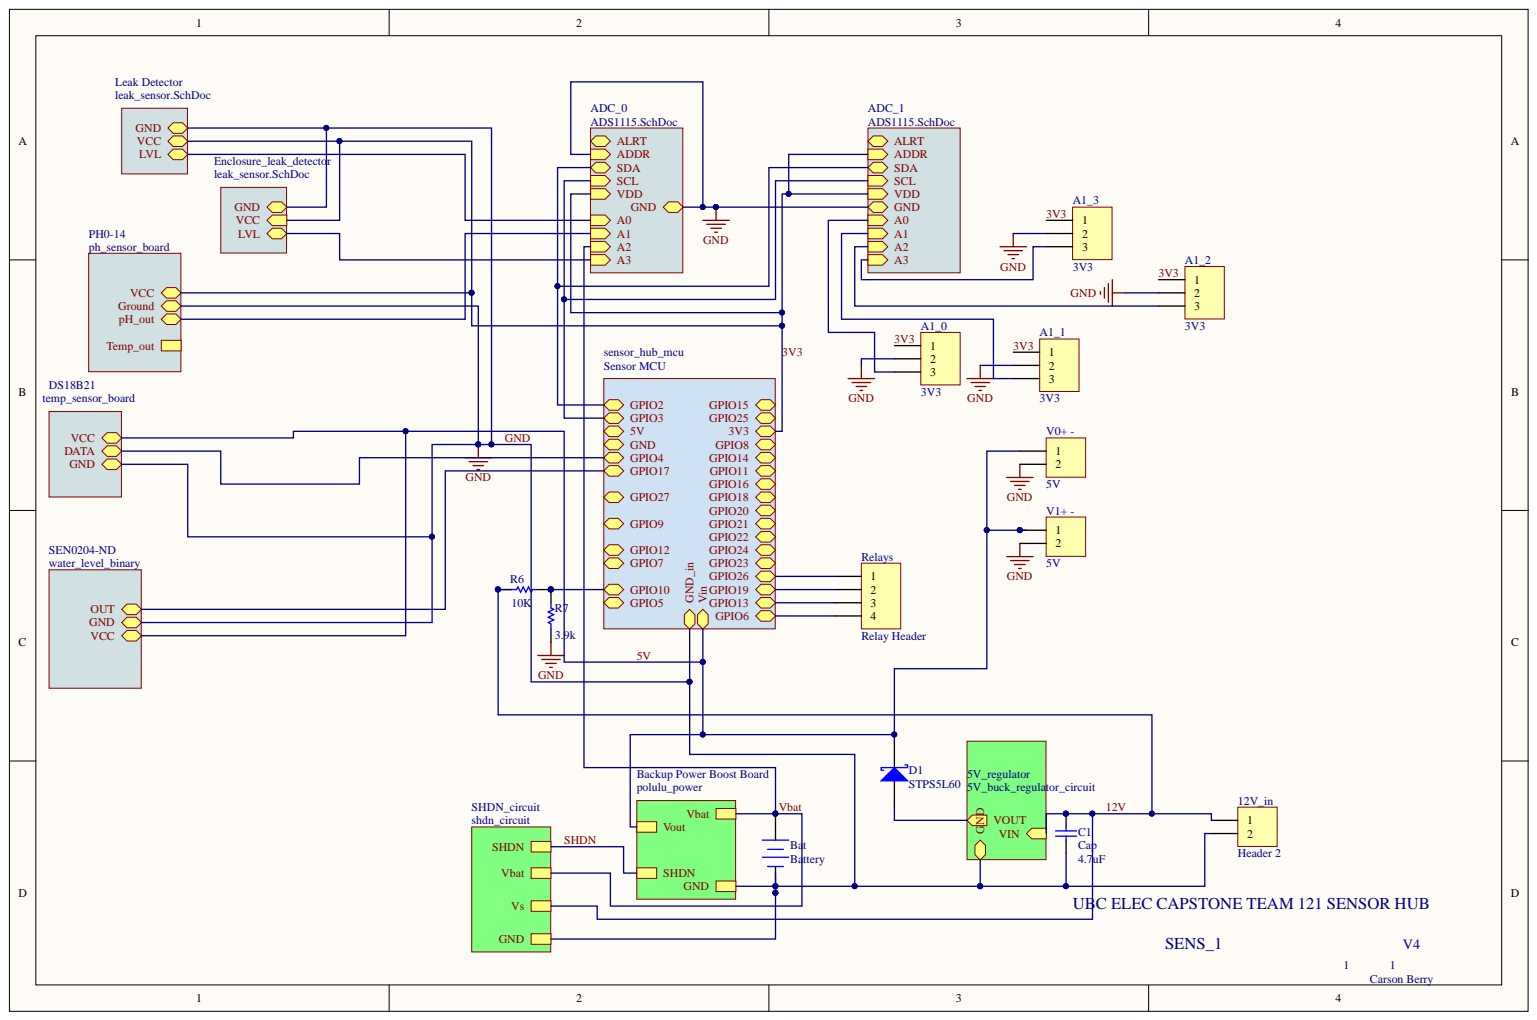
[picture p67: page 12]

Enclosure_leak_detector leak_sensor.SchDoc

SCL

GND

GND R6

10K | R7 | | GPIO5 GPIO13 GPIO6 | 3 4

Backup Power Boost Board
polulu_power

UBC ELEC CAPSTONE TEAM 121 SENSOR HUB


Comment | Description | Designator | Footprint | LibRef | Quantity
Header 2 | Power 12V in | 12V_in | 2_channel_termina l_block | Header 2 | 1
3V3 | Header, 3-Pin | A1_0, A1_1, A1_2, A1_3 | 3_channel_termina l_block | Header 3 | 4
ADS1*15 | Header, 10-Pin | ADC_1_ADC_0, ADC_1_ADC_1 | HDR1X10 | Header 10 | 2
Battery | 2AA batteries | Bat | BAT-2 | Battery | 1
Header 4 | Header, 4-Pin | Boost_0, Boost_1 | HDR1X4 | Header 4 | 2
Cap | Capacitor | C1 | RAD-0.3 | Cap | 1
STPS5L60 | Power Schottky rectifier, 60 V, 5 A, 2-Pin DO-201AD, RoHS, Cut Tape | D1 | STM-DO-201AD | CMP-2000-05365-1 | 1
Leak Sensor | Header, 3-Pin | Leak_Enclosure_le ak_detector, Leak_Leak Detector | 3_channel_termina l_block | Header 3 | 2
Header 20X2 | GPIO shield for RPi | P12 | HDR2X20 | Header 20X2 | 1
pH Sensor | Header, 4-Pin | pH | 4_channel_termina l_block | Header 4 | 1
2N3904 | NPN General Purpose Amplifier | Q1 | TO-92A | 2N3904 | 1
Res1 | Resistor | R1, R2, R3, R4, R6, R7 | AXIAL-0.3 | Res1 | 6
| Pull up | R5 | AXIAL-0.3 | Res1 | 1
Relay Header | Relay Control | Relays | 4_channel_termina l_block | Header 4 | 1
RPi Power | Power Pins | RPi Vin | HDR1X2 | Header 2 | 1
Temp Sensor | Header, 3-Pin | Temp | HDR1X3 | Header 3 | 1
5V | Header, 2-Pin | V0+ -, V1+ - | 2_channel_termina l_block | Header 2 | 2
Volt Reg | Voltage Regulator | VR1 | D2PAK_N | Volt Reg | 1
Volt Reg | Voltage Regulator | VR2 | D2PAK_M | Volt Reg | 1
WL Sensor | Header, 3-Pin | Water_level | 3_channel_termina l_block | Header 3 | 1
